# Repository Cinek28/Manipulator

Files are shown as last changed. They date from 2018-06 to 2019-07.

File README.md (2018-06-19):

# Manipulator
Repository designated for master's degree thesis development on manipulator's control problems. The thesis is conducted on real-life model of 6 DOF manipulator designated to work on Mars rover platform.

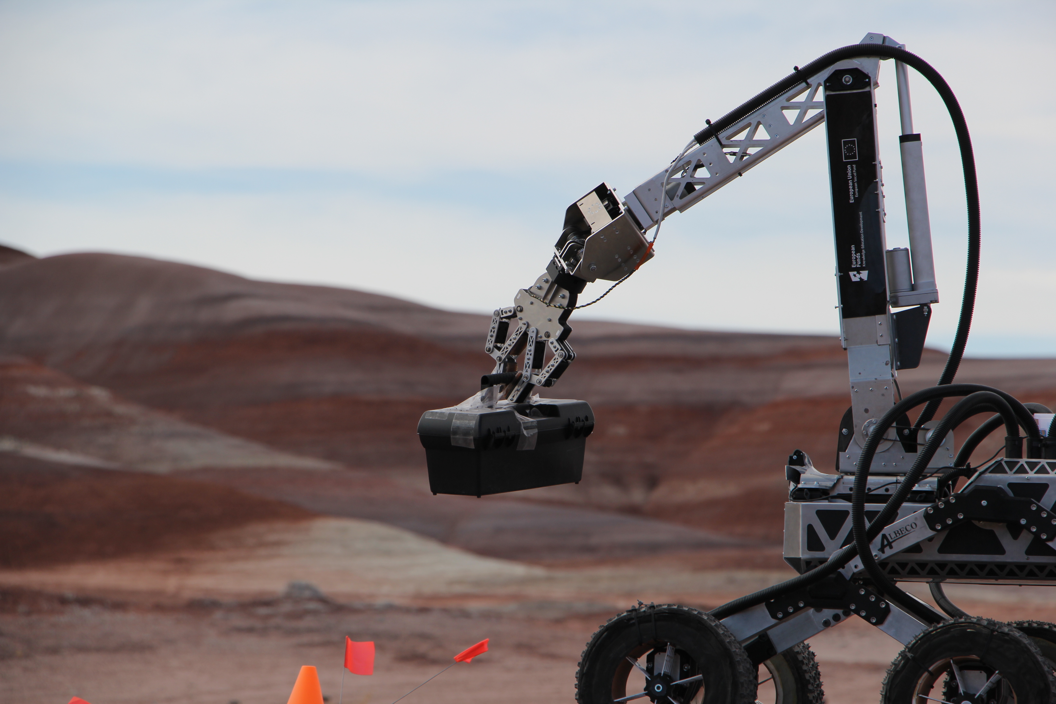
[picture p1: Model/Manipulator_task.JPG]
Manipulator working in designated environment on URC2018 competition.


List of folders:
1. Application: Contains project files of desktop app for controlling manipulator using UART connection.
2. Model: Contains renders and .stl files with whole manipulator model (able to open in CAD programs). Also a quick report of mechanical and electronic design of manipulator.
3. STM32F407: Folder containing Atollic TrueStudio project files and source code being developed for STM32F407RET microcontroller used to control manipulator
4. Simulation: Folder containing ROS files for simulation of manipulator's kinematics in Gazebo.
5. Thesis: Contains Latex files of the thesis.

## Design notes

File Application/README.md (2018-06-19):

# Application
Folder contains project files of desktop app, which is being desinged to use in order to control manipulator via UART/SSH connection. First app was written in C# (pic attached). Application in development will be written in C++ using Qt.

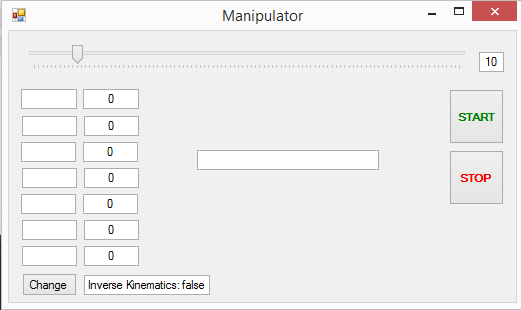
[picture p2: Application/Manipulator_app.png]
First control application for manipulator


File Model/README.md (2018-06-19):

# Model
Folder contains renders and pictures of manipulator. The review of mechanical and electronic design is called "Raport.pdf". Due to the fact that .stl file is large (> 100 MB) it is not held in remote repo. (STL file enables to view model in CAD programs)

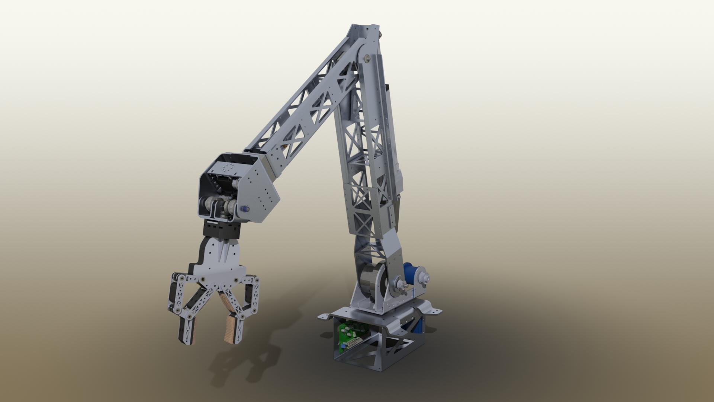
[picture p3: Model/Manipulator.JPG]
Render of manipulator's CAD model


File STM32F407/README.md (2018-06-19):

# STM32F407
The program written for STM32F407RET microcontroller using Atollic TrueStudio designed for controlling manipulator.

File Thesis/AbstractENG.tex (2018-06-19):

\externaldocument{CH_Wstep}
\externaldocument{CH_Opis_konstrukcji}
\externaldocument{CH_Model}
\externaldocument{CH_EKF}
\externaldocument{CH_Algorytm}

\begin{center}
\textbf{Abstract}
\end{center}
\paragraph{Implementation of Bellman-Ford algorithm for maze-solving by micromouse type robot}
\paragraph{}
The aim of this thesis was solving the shortest path problem for a maze described in the Micromouse competition rules along with the implementation of a chosen algorithm on a mobile robot. The document presents detailed description of project with the quality assessment of applied methods. First chapter shows requirements for Micromouse competition (Chapter 1). Based on the rules, a mechanical and electronic platform of mobile robot was developped (Chapter 2). Next step was to obtain mathematical model of given differential-drive robot (Chapter 3) which was used in chosen approach. These equations are essential in determining the position based on previously known location and measurements acquired from sensors installed on the platform. In order to localize the robot, a SLAM algorithm using Extended Kalman Filter was implemented (Chapter 4). The afore mentioned filter is recommended for estimating non- linear processes and enables the use of sensor fusion. This method gives an optimal information about process state. It is possible to point out where in the maze the robot is. Created map of environment is used in Bellman-Ford algorithm for finding the shortest path through the maze (Chapter 5). The final stage of the project was to conduct experiments in order to assess if the methods used were correct. Based on obtained results the weaknesses and possible improvements were summarized (Chapter 6).
\vspace*{\baselineskip}

\noindent\textbf{Keywords:} \textit{Micromouse, mobile robot, Bellman-Ford algorithm, shortest path problem, Extended Kalman Filter, localization}

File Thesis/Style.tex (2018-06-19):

%jezyk dokumentu
\usepackage[utf8]{inputenc}
\usepackage[T1]{fontenc}
\usepackage[T1]{polski}
\usepackage[english, polish]{babel}
%\setlanguage{polish}
\usepackage{fullpage}
\usepackage{pdfpages}
%Style
\usepackage{siunitx,booktabs,threeparttable,caption}
\captionsetup[table]{justification=raggedright,singlelinecheck=off}
\sisetup{separate-uncertainty=true}

\captionsetup[figure]{justification=centering,singlelinecheck=off}
\sisetup{separate-uncertainty=true}

\setlength\parindent{0.5cm}
\renewcommand{\baselinestretch}{1.15} 
\makeatletter
\def\ps@myPS{%
    \def\@oddfoot{\null\hfill\thepage}
    \def\@evenfoot{\thepage}%
    \def\@evenhead{\null\hfil\slshape\leftmark}%
    \def\@oddhead{{\slshape\rightmark}}}%
\makeatother
\makeatletter
\renewcommand\chapter{\if@openright\cleardoublepage\else\clearpage\fi
                    \thispagestyle{myPS}%
                    \global\@topnum\z@
                    \@afterindentfalse
                    \secdef\@chapter\@schapter}
\makeatother
\pagestyle{myPS}
%linkowanie
\usepackage{hyperref}
\hypersetup{
    colorlinks,
    citecolor=black,
    filecolor=black,
    linkcolor=black,
    urlcolor=black
}
\usepackage{multicol}
\usepackage{caption}
\usepackage{subcaption}
%math
\usepackage{amsmath}
\usepackage{gensymb}
\def\deg {$^o$\ }
\newcommand{\mat}[1]{\mathbf{#1}} % undergraduate algebra version
\newcommand{\sub}[1]{\footnotesize #1 \normalsize}
%bibliografia
\usepackage{csquotes}
\usepackage[backend=biber]{biblatex}
%,style=authoryear
%\renewcommand{\cite}[1]{\parencite{#1}}
\usepackage{float}
%numeracja
\usepackage{chngcntr}
%\counterwithout{figure}{chapter}	%numeracja ciagła
%oblsuga grafiki
\usepackage{graphicx}
\graphicspath{{../img/}{}../image/}
%time and date management
\usepackage{datetime}
\newcommand{\miesiac}{%
  \ifcase\THEMONTH
  \or Styczeń% 1
  \or Luty% 2
  \or Marzec% 3
  \or Kwiecień% 4
  \or Maj% 5
  \or Czerwiec% 6
  \or Lipiec% 7
  \or Sierpień% 8
  \or Wrzesień% 9
  \or Październik% 10
  \or Listopad% 11
  \or Grudzień% 12
  \fi}
\newdateformat{mmyyyy}{\miesiac \  \THEYEAR}

%zarzadzanie tekstem
\brokenpenalty=1000		% nie dziel wyrazów miedzy stronami
\clubpenalty=1000		% kara za sierotki
\widowpenalty=10000		% nie pozostawiaj wdów

\usepackage[inner=30mm,outer=20mm,top=25mm,bottom=25mm]{geometry}

%Wyliczenia:
\usepackage{enumerate}
%Fragmenty kodu:
\usepackage{listings}
\usepackage{color}

\definecolor{dkgreen}{rgb}{0,0.6,0}
\definecolor{gray}{rgb}{0.5,0.5,0.5}
\definecolor{mauve}{rgb}{0.58,0,0.82}

\lstset{frame=tb,
  language=C,
  aboveskip=3mm,
  belowskip=3mm,
  showstringspaces=false,
  columns=flexible,
  basicstyle={\small\ttfamily},
  numbers=none,
  numberstyle=\tiny\color{gray},
  keywordstyle=\color{blue},
  commentstyle=\color{dkgreen},
  stringstyle=\color{mauve},
  breaklines=true,
  breakatwhitespace=true,
  tabsize=3
}

\usepackage{xr}
\usepackage{amsfonts}
\defbibheading{myheading}[Bibliografia]{%
  \chapter*{#1}
  \addcontentsline{toc}{chapter}{#1}}

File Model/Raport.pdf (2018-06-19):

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

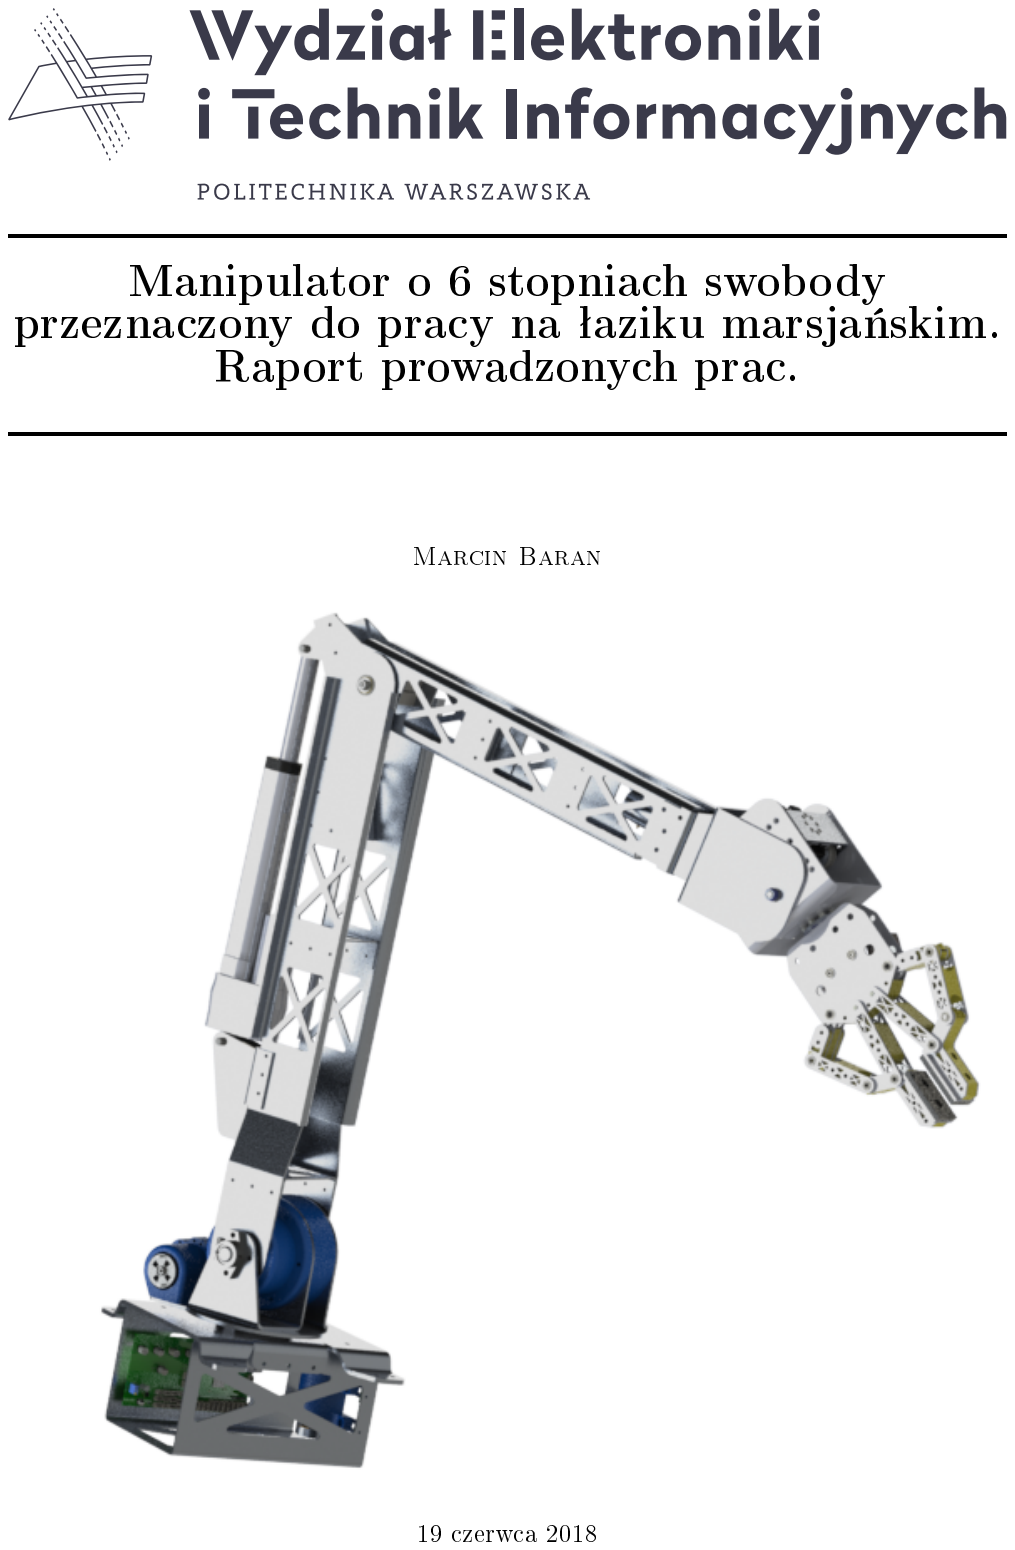
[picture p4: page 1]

# Spis tre±ci

## 0.1 Wst¦p

Manipulator zostaª skonstruowany oraz zbudowany z my±l¡ o pracy na ªaziku marsja«skim- projekcie Koªa Naukowego Robotyków realizowanego na zawody URC 2018. W obecnym etapie prac zako«czono monta» konstrukcji wykonanej z aluminium i ABS-X oraz przygotowano elektronik¦ potrzebn¡ do sterowania i zasilania nap¦dami ka»dego z czªonów mechanizmu. Manipulator b¦dzie tak»e platform¡ do badania efektywno±ci sterowania mechanizmu wieloczªonowego za pomoc¡ ró»nego typu regulatorów.

## 0.2 Mechanika

Manipulator posiada 6 stopni swobody realizowanych za pomoc¡:

- Stopie« I: Obrót podstawy

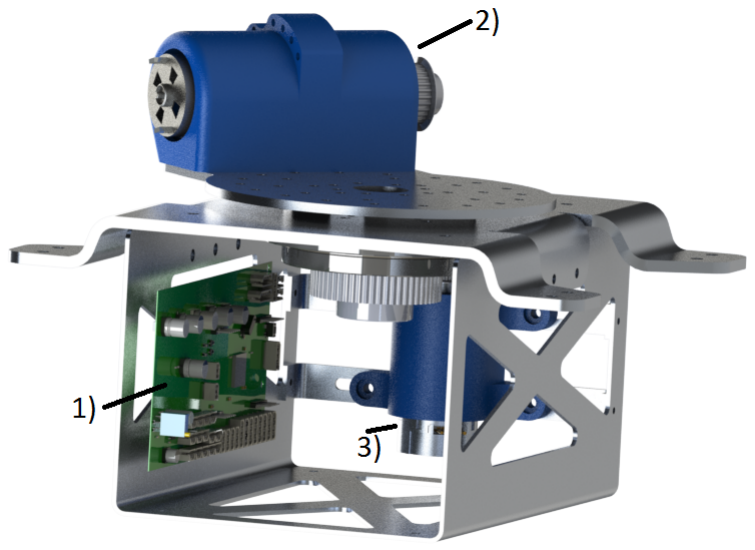
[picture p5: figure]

Obrót podstawy manipulatora realizowany jest za pomoc¡ silnika DC Pololu z przekªadni¡ 37Dx73L 131:1 zasilanym napi¦ciem 12V osi¡gaj¡cy pr¦dko±¢ obrotow¡ 80RPM (https://botland.com.pl/silniki-dc-z-przekladnia-i-enkoderami/5114-silnik-z-przekladnia-37dx73l-1311-enkoder-cpr-64.html) (https://botland.com.pl/silniki-dc-z-przekladnia-i-enkoderami/5114-silnik-z-przekladnia-37dx73l-1311-enkoder-cpr-64.html) (na powy»szej grace zaznaczony numerem 3). Przeªo»enie nap¦du na obrót podstawy jest realizowane za pomoc¡ paska HTD 3M oraz kóª z¦batych. Dodatkowo w podstawie manipulatora znajduje si¦ sterownik nap¦dów (oznaczony jako 1) pozwalaj¡cy na zasilanie oraz sterowanie wszystkimi nap¦dami za pomoc¡ sterowania sygnaªem PWM.

- Stopie« II: Obrót ramion

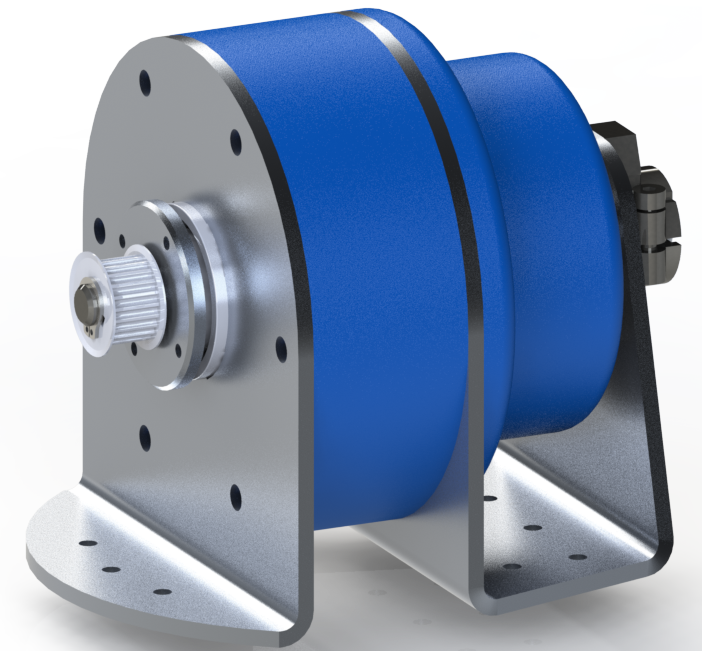
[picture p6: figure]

Obrót ramion realizowany jest za pomoc¡ przekªadni falowej o przeªo»eniu 159:1 oraz silnika od wkr¦tarki Bosch zasilanego napi¦ciem 12V (oznaczony na poprzedniej grace jako 2). Tutaj tak»e do poª¡czenia nap¦du z przekªadni¡ u»yto paska HTD oraz kóª z¦batych.

- Stopie« III: Obrót przedramienia

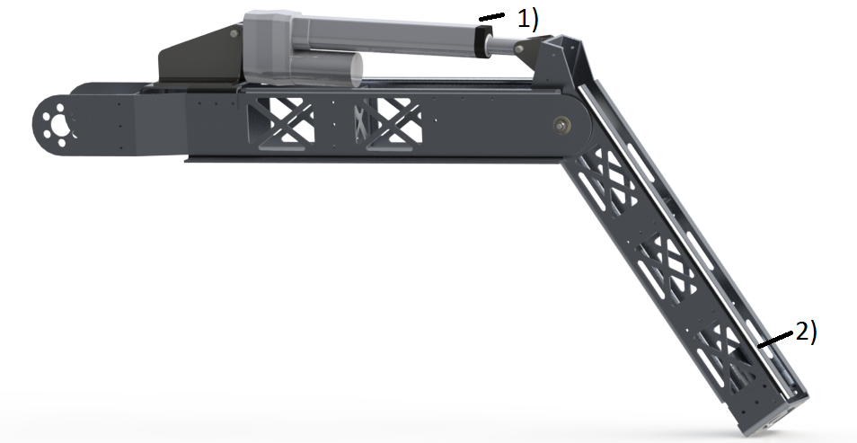
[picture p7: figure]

Obrót przedramienia wykonywany jest za pomoc¡ siªownika liniowego DSZY1 nap¦dzanego silnikiem DC 12V (http://www.drive-system.com/pdf/en/DC_Linearactuator_DSZY1_poti.pdf) o maksymalnym obci¡»eniu 1000N. (na grace zaznaczony jako 1).

- Stopie« IV: Obrót ki±ci

Obrót ki±ci sferycznej (nadgarstek) realizowany jest za pomoc¡ silnika DC Pololu z przekªadni¡ 37Dx73L 131:1 zasilanym napi¦ciem 12V osi¡gaj¡cy pr¦dko±¢ obrotow¡ 80RPM (https://botland.com.pl/silniki-dc-z-przekladnia-i-enkoderami/5114-silnik-z-przekladnia-37dx73l-1311-enkoder-cpr-64.html) (https://botland.com.pl/silniki-dc-z-przekladnia-i-enkoderami/5114-silnik-z-przekladnia-37dx73l-1311-enkoder-cpr-64.html) ( na grace powy»ej zaznaczone jako 2) poª¡czonego bezpo±rednio z ªo»yskiem obrotowym przymocowanym do ki±ci.

- Stopie« V i VI: Ki±¢ sferyczna

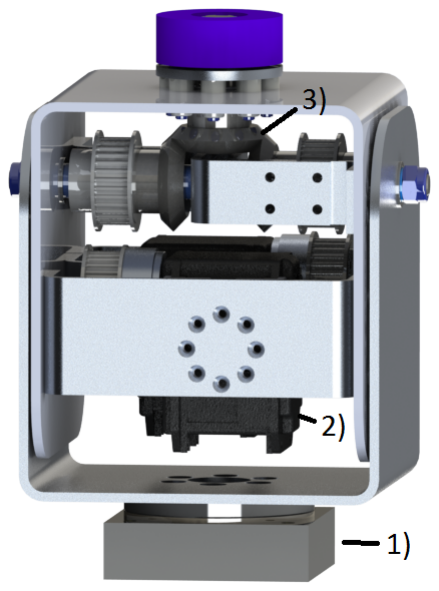
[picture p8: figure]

Ki±¢ sferyczna, czyli taka, w której osie obrotów czªonów pokrywaj¡ si¦ w jednym punkcie, zostaªa skonstruowana z wykorzystaniem mechanizmu ró»nicowego (dyferencjaªu) (3). Mechanizm nap¦dzany jest za pomoc¡ serw Dynamixel RX-64 o napi¦ciu zasilania od 15 do 18 V oraz momencie znamionowym 5.6 Nm (2) (http://www.trossenrobotics.com/dynamixel-rx-64-robotactuator.aspx). (http://www.trossenrobotics.com/dynamixel-rx-64-robot-actuator.aspx) Zastosowanie ki±ci sferycznej w znacznym stopniu uªatwia rozwi¡zanie zadania odwrotnego kinematyki pozwalaj¡cego na implementacj¦ sterowania w wygodniejszych wspóªrz¦dnych zwi¡zanych z narz¦dziem, a nie poszczególnymi czªonami.

## 0.3 Schemat elektroniczny

W celu zasilania nap¦dów manipulatora, a tak»e ich sterowania zostaªy zaprojektowane 2 pªytki PCB: sterownik nap¦dów oraz nakªadka pod pªytk¦ STM32 NUCLEO-F446RE, która posªu»y do sterowania, komunikacji oraz rozwi¡zywania zadania odwrotnego kinematyki. Jako sygnaª sprz¦»enia zwrotnego do regulatora nap¦dów posªu»y odczytywany z enkoderów magnetycznych, zamontowanych na ka»dym z czªonów, k¡t obrotu. W projekcie zastosowano enkodery rmy AMS: https://ams.com/kor/content/download/1285/7214/file/AS5040_DS000374_3-00.pdf. (https://ams.com/kor/content/download/1285/7214/file/AS5040_DS000374_3-00.pdf) Pozwala on na wyznaczanie absolutnej pozycji, co oznacza, »e nawet po wyª¡czeniu zasilania manipulatora i ponownym jego wª¡czeniu b¦dzie mo»-liwe wyznaczenie dokªadnej konguracji mechanizmu. Komunikacja z komputerem pokªadowym ªazika odbywa¢ si¦ b¦dzie za pomoc¡ interfejsu CAN. Do komunikacji z komputerem w celach implementacji oprogramowania zastosowany zostanie interfejs UART.

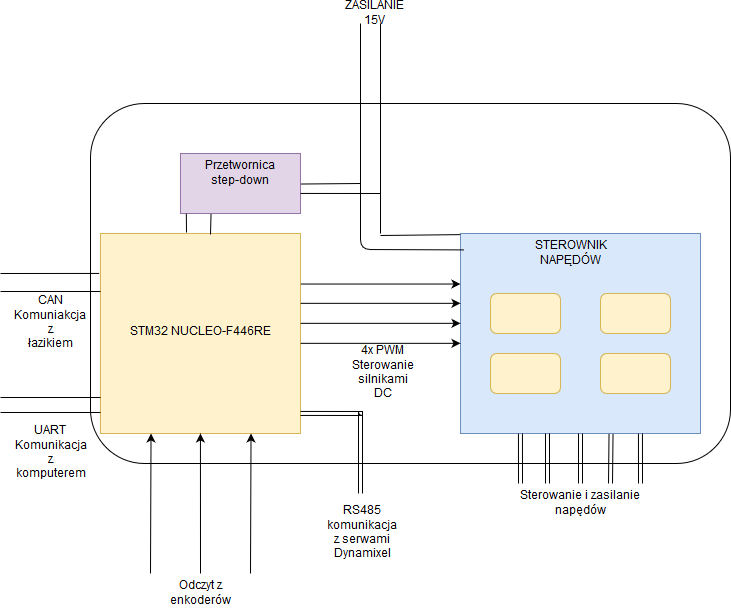
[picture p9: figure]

## 0.4 Sterowanie

Na tym etapie zostaªo stworzone oprogramowanie steruj¡ce pozwalaj¡ce na sterowanie we wspóªrz¦dnych zª¡czowych oraz kod pozwalaj¡cy na zastosowanie kinematyki odwrotnej w celu sterowania we wspóªrz¦dnych narz¦dziowych (zwi¡zanych z chwytakiem). W tej chwili trwa integracja czujników magnetycznych (enkoderów) w celu wyliczania pr¦dko±ci czªonów i zako«czenia implementacji programu steruj¡cego.

## 0.5 Plan dalszych prac

Prace nad oprogramowaniem i symulacj¡ pracy manipulatora zostaªy opó¹nione ze wzgl¦du na konieczno±¢ poprawy konstrukcji mechanicznej w okresie kwiecie«-czerwiec. Na ten moment prace nad konstrukcj¡ mechaniczn¡ zostaªy zako«czone. Plan pracy przedstawia si¦ nast¦puj¡co:

- do 30 czerwca: uko«czenie integracji enkoderów magnetycznych
- do 15 lipca: utworzenie modelu manipulatora w Gazebo - przesªanie kolejnego raportu
- do 30 lipca: przeprowadzenie symulacji dziaªania mechanizmu w Gazebo
- do 15 sierpnia: uko«czenie pisania programu steruj¡cego manipulatorem
- do 30 sierpnia: napisanie aplikacji desktopowej do sterowania i debugowania pracy manipulatora -
| przesªanie kolejnego raportu
- od wrze±nia: badanie i dostosowywanie metod sterowania (cz¦±¢ badawcza)
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

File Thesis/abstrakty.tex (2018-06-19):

%!TeX spellcheck = pl_PL
\documentclass[11pt, a4paper, twoside]{report}

\input{Style.tex}
\addbibresource{./Bibliografia/books.bib}
%\addbibresource{../bib/articles.bib}
\addbibresource{./Bibliografia/online.bib}

\begin{document}
%\input{nauka.tex}

%\input{TitlePage2017.tex}
%\newpage\null\thispagestyle{empty}
%\newpage\null\thispagestyle{empty}
%\input{AbstractPL.tex}
%\newpage\null\thispagestyle{empty}
%\newpage\null\thispagestyle{empty}
\pagenumbering{gobble}
\input{AbstractPL.tex}

%\newpage\null\thispagestyle{empty}
%\input{Oswiadczenie.tex}
%\newpage\null\thispagestyle{empty}

%\tableofcontents
%\thispagestyle{empty}

%\addtocontents{toc}{\protect%\thispagestyle{empty}}

%\input{CH_Wstep.tex}
%\input{CH_Opis_konstrukcji.tex}
%\input{CH_Model.tex}
%\input{CH_EKF.tex}
%\input{CH_Algorytm.tex}
%\input{CH_Wnioski.tex}

%\cleardoublepage
%bibliograpy
%bibintoc
%\printbibheading[title={Bibliography},heading=bibnumbered]
%\nocite{*}
%\printbibliography[heading=myheading]

%\clearpage
%\addcontentsline{toc}{chapter}%{\listfigurename}
%\listoffigures

%\addcontentsline{toc}{chapter}%{\listtablename}
%\listoftables

%\appendix
%\input{CH_Zalaczniki.tex}

\end{document}

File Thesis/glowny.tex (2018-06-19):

%!TeX spellcheck = pl_PL
\documentclass[11pt, a4paper, twoside]{report}

\input{Style.tex}
\addbibresource{./Bibliografia/books.bib}
%\addbibresource{../bib/articles.bib}
\addbibresource{./Bibliografia/online.bib}

\begin{document}

%\input{TitlePage2018.tex}
%\newpage\null\thispagestyle{empty}
%\newpage\null\thispagestyle{empty}
\input{AbstractPL.tex}
\newpage\null\thispagestyle{empty}
\newpage\null\thispagestyle{empty}
\input{AbstractENG.tex}
\newpage\null\thispagestyle{empty}
\input{Oswiadczenie.tex}
\newpage\null\thispagestyle{empty}

\tableofcontents
\thispagestyle{empty}

\addtocontents{toc}{\protect\thispagestyle{empty}}

\input{CH_Wstep.tex}
\input{CH_Stan_wiedzy.tex}
\input{CH_Opis_konstrukcji_manipulatora.tex}
\input{CH_Model_kinematyki_manipulatora.tex}
\input{CH_Symulacja_konstrukcji_w_środowisku_Gazebo.tex}
\input{CH_Program_sterujacy_ruchem_robota.tex}
\input{CH_Badanie_jakości_sterowania.tex}
\input{CH_Wnioski.tex}

\cleardoublepage
%bibliograpy
%bibintoc
%\printbibheading[title={Bibliography},heading=bibnumbered]
\nocite{*}
\printbibliography[heading=myheading]

\clearpage
\addcontentsline{toc}{chapter}{\listfigurename}
\listoffigures

\addcontentsline{toc}{chapter}{\listtablename}
\listoftables

\appendix
%\input{CH_Zalaczniki.tex}

\end{document}

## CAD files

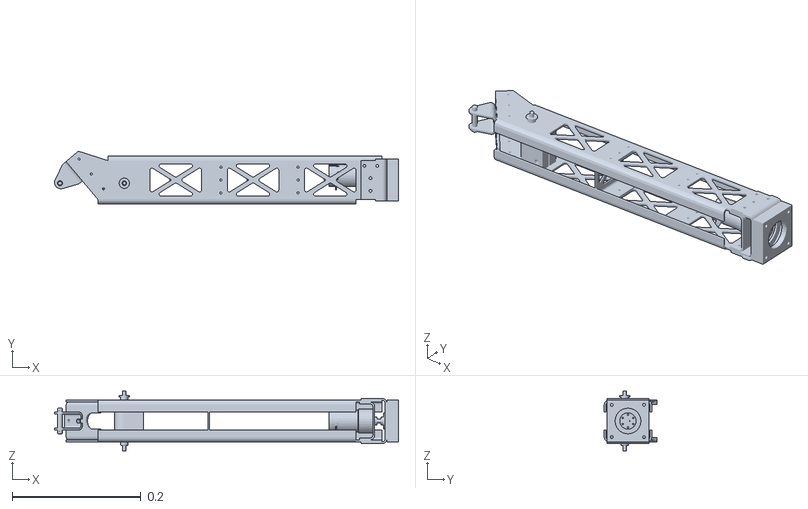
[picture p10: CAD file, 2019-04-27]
Simulation/src/manipulator/meshes/arm_link.STL
0.534 x 0.0818 x 0.0925

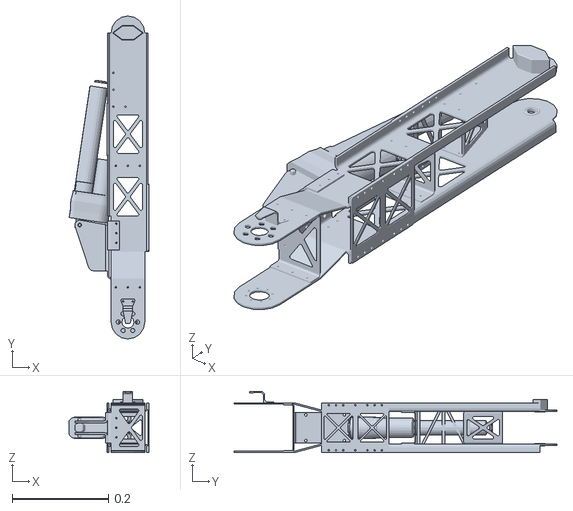
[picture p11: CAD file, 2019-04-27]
Simulation/src/manipulator/meshes/forearm_link.STL
0.165 x 0.67 x 0.127

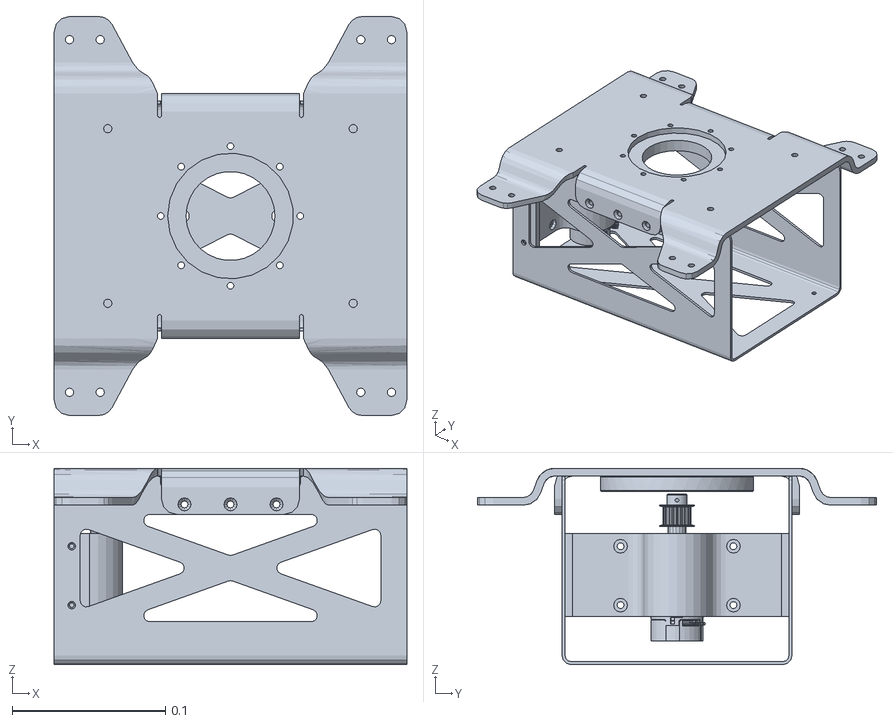
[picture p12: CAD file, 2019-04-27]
Simulation/src/manipulator/meshes/base_link.STL
0.23 x 0.26 x 0.128

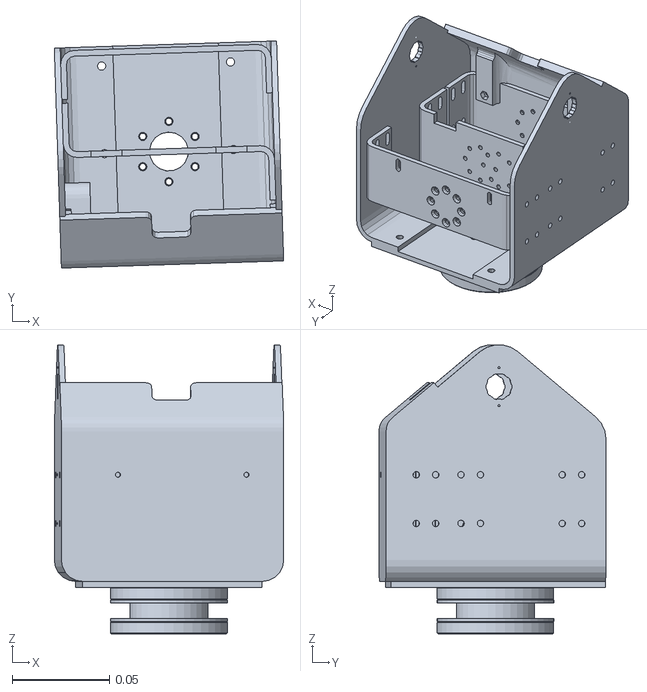
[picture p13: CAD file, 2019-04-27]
Simulation/src/manipulator/meshes/wrist_rotation_link.STL
0.118 x 0.117 x 0.148

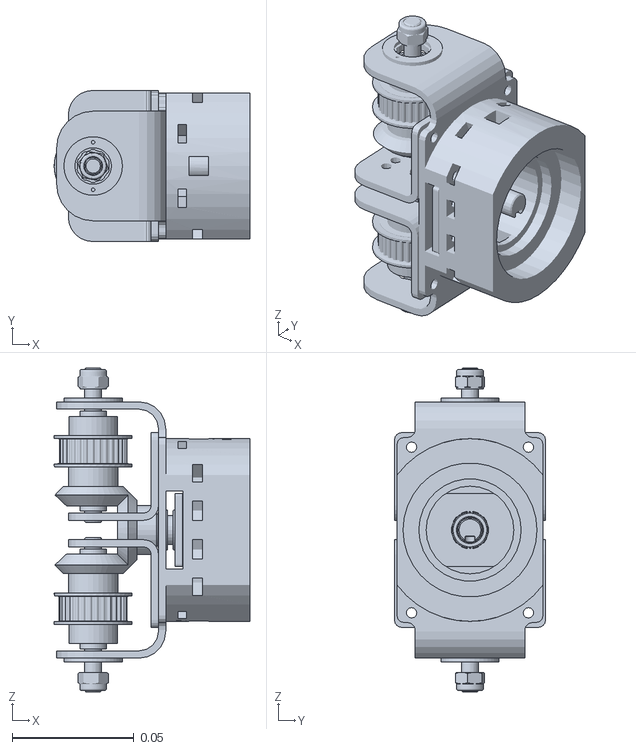
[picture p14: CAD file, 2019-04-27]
Simulation/src/manipulator/meshes/wrist_pitch_link.STL
0.0803 x 0.062 x 0.133

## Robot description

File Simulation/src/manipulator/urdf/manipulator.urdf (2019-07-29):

<robot name="manipulator">

  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
  <link name="world"/>

  <joint name="fixed" type="fixed">
    <parent link="world"/>
    <child link="base_link"/>
  </joint>

  <link name="base_link">
    <inertial>
      <origin xyz="-0.029 3.0957E-06 0.081458" rpy="0 0 0" />
      <mass value="1.404" />
      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
    </inertial>
    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
  </link>

 <link name="shoulder_link">
    <inertial>
      <origin xyz="-0.024603 0.0034265 0.064143" rpy="0 0 0" />
      <mass value="4.1214" />
      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
    </inertial>
    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
  </link>

  <joint name="shoulder_rotation" type="revolute">
    <origin xyz="0 0 0.13" rpy="0 0 0" />
    <parent link="base_link" />
    <child link="shoulder_link" />
    <axis xyz="0 0 1" />
    <limit lower="-3.14" upper="3.14" effort="50" velocity="8.3776" />
  </joint>

  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

  <link name="forearm_link">
    <inertial>
      <origin xyz="-0.030709 0.2846 0.0021162" rpy="0 0 0" />
      <mass value="2.138" />
      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
    </inertial>
    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
  </link>

  <joint name="forearm_rotation" type="revolute">
    <origin xyz="0 0.00175 0.0705" rpy="1.5708 0 0" />
    <parent link="shoulder_link" />
    <child link="forearm_link" />
    <axis xyz="0 0 -1" />
    <limit lower="-0.90" upper="1.3963" effort="500" velocity="1.2" />
  </joint>

  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

  <link name="arm_link">
    <inertial>
      <origin xyz="0.1767 0.0069722 5.0223E-06" rpy="0 0 0" />
      <mass value="1.1195" />
      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
    </inertial>
    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
  </link>

  <joint name="arm_rotation" type="revolute">
    <origin xyz="0 0.6 0" rpy="0 0 -1.3089" />
    <parent link="forearm_link" />
    <child link="arm_link" />
    <axis xyz="0 0 -1" />
    <limit lower="-2.5" upper="0" effort="500" velocity="0.2" />
  </joint>

  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

  <link name="wrist_rotation_link">
    <inertial>
      <origin xyz="0.00022986 -0.0044455 0.068045" rpy="0 0 0" />
      <mass value="0.70662" />
      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
    </inertial>
    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
  </link>

  <joint name="wrist_rotation" type="revolute">
    <origin xyz="0.408 0.005 0" rpy="0 1.5708 0" />
    <parent link="arm_link" />
    <child link="wrist_rotation_link" />
    <axis xyz="0 0 -1" />
    <limit lower="-3.14" upper="3.14" effort="18" velocity="8.3776" />
  </joint>

 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

  <link name="wrist_pitch_link">
    <inertial>
      <origin xyz="0.02283 1.6924E-05 4.4001E-05" rpy="0 0 0" />
      <mass value="0.22279" />
      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
    </inertial>
    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
  </link>

  <joint name="wrist_pitch" type="revolute">
    <origin xyz="0 0 0.129" rpy="-1.5708 0 1.603" />
    <parent link="wrist_rotation_link" />
    <child link="wrist_pitch_link" />
    <axis xyz="0 0 -1" />
    <limit lower="0" upper="3.14" effort="10.8" velocity="5.236" />
  </joint>

 <link name="gripper_link">
    <inertial>
      <origin xyz="0.00062878 0.0062787 0.096632" rpy="0 0 0" />
      <mass value="0.52227" />
      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
    </inertial>
    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
  </link>

  <joint name="gripper_rotation" type="revolute">
    <origin xyz="0.0643 0 0" rpy="0 1.5708 0" />
    <parent link="wrist_pitch_link" />
    <child link="gripper_link" />
    <axis xyz="0 0 -1" />
    <limit lower="-3.14" upper="3.14" effort="10.8" velocity="5.236" />
  </joint>

  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

</robot>

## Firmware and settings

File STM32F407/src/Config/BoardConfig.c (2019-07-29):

/*
 * BoardConfig.c
 *
 *  Created on: 21.07.2019
 *      Author: Cinek
 */

#include "BoardConfig.h"

uint8_t RCC_CONF()
{
	// Setting HSE with 8MHz external oscillator as main clock:
	RCC_DeInit();

	RCC_HSEConfig(RCC_HSE_ON);
	while(RCC_WaitForHSEStartUp() != SUCCESS);

	// Setting frequency to 144 MHz:
	RCC_PLLConfig(RCC_PLLSource_HSE, 4, 144, 2, 4);
	RCC_HCLKConfig(RCC_SYSCLK_Div1);
	// PCLK1 peripherals at 36 MHz:
	RCC_PCLK1Config(RCC_HCLK_Div4);
	// PCLK2 peripherals at 72 MHz:
	RCC_PCLK2Config(RCC_HCLK_Div2);
	RCC_SYSCLKConfig(RCC_SYSCLKSource_PLLCLK);
	//SysTick initialisation to 1000 Hz:
//	SysTick_Config(SYSTIC_CNT);

	SystemCoreClockUpdate();

	RCC_ClocksTypeDef RCC_Clocks;
	RCC_GetClocksFreq(&RCC_Clocks);
	if(RCC_Clocks.HCLK_Frequency != CORE_CLK_FREQ)
		return -1;
	else if(SystemCoreClock != CORE_CLK_FREQ)
		return -2;
	else if(RCC_Clocks.HCLK_Frequency != 36000000)
		return -3;
	else if(RCC_Clocks.HCLK_Frequency != 72000000)
		return -4;

	RCC_PLLCmd(ENABLE);
	while(RCC_GetFlagStatus(RCC_FLAG_PLLRDY) != SET);
	return 0;
};

void GPIO_MOTOR_CONF(){

	RCC_AHB1PeriphClockCmd(RCC_AHB1Periph_GPIOA, ENABLE);
	RCC_AHB1PeriphClockCmd(RCC_AHB1Periph_GPIOB, ENABLE);
	RCC_AHB1PeriphClockCmd(RCC_AHB1Periph_GPIOC, ENABLE);
	RCC_AHB1PeriphClockCmd(RCC_AHB1Periph_GPIOD, ENABLE);
	RCC_AHB1PeriphClockCmd(RCC_AHB1Periph_GPIOE, ENABLE);

	//MOTOR_1_PWM:

	GPIO_InitTypeDef GPIO_InitStructure;
	GPIO_InitStructure.GPIO_Pin = GPIO_Pin_8;
	GPIO_InitStructure.GPIO_OType = GPIO_OType_PP;
	GPIO_InitStructure.GPIO_PuPd = GPIO_PuPd_NOPULL;
	GPIO_InitStructure.GPIO_Mode = GPIO_Mode_AF;
	GPIO_InitStructure.GPIO_Speed = GPIO_Speed_100MHz;
	GPIO_Init(GPIOB, &GPIO_InitStructure);
	GPIO_PinAFConfig(GPIOB, GPIO_PinSource8, GPIO_AF_TIM4);

	//MOTOR_2_PWM:

	GPIO_InitStructure.GPIO_Pin = GPIO_Pin_2;
	GPIO_Init(GPIOA, &GPIO_InitStructure);
	GPIO_PinAFConfig(GPIOA, GPIO_PinSource2, GPIO_AF_TIM2);

	GPIO_InitStructure.GPIO_Pin = GPIO_Pin_6;
    GPIO_Init(GPIOA, &GPIO_InitStructure);
	GPIO_PinAFConfig(GPIOA, GPIO_PinSource6, GPIO_AF_TIM3);

	//MOTOR_3_PWM:

	GPIO_InitStructure.GPIO_Pin = GPIO_Pin_3;
	GPIO_Init(GPIOA, &GPIO_InitStructure);
	GPIO_PinAFConfig(GPIOA, GPIO_PinSource2, GPIO_AF_TIM2);

	//MOTOR_4_PWM:

	GPIO_InitStructure.GPIO_Pin = GPIO_Pin_15;
	GPIO_Init(GPIOA, &GPIO_InitStructure);
	GPIO_PinAFConfig(GPIOA, GPIO_PinSource15, GPIO_AF_TIM2);

	//MOTOR_5_PWM:

	GPIO_InitStructure.GPIO_Pin = GPIO_Pin_3;
	GPIO_Init(GPIOB, &GPIO_InitStructure);
	GPIO_PinAFConfig(GPIOB, GPIO_PinSource3, GPIO_AF_TIM2);

	//MOTOR_6_PWM:

	GPIO_InitStructure.GPIO_Pin = GPIO_Pin_9;
	GPIO_Init(GPIOB, &GPIO_InitStructure);
	GPIO_PinAFConfig(GPIOB, GPIO_PinSource9, GPIO_AF_TIM4);

	//BM_PWM:

	GPIO_InitStructure.GPIO_Pin = GPIO_Pin_10;
	GPIO_Init(GPIOB, &GPIO_InitStructure);
	GPIO_PinAFConfig(GPIOB, GPIO_PinSource10, GPIO_AF_TIM2);

	GPIO_InitStructure.GPIO_Pin = GPIO_Pin_11;
	GPIO_Init(GPIOB, &GPIO_InitStructure);
	GPIO_PinAFConfig(GPIOB, GPIO_PinSource11, GPIO_AF_TIM2);

	//Servo PWM:

	GPIO_InitStructure.GPIO_Pin = GPIO_Pin_4 | GPIO_Pin_5;
	GPIO_Init(GPIOB, &GPIO_InitStructure);
	GPIO_PinAFConfig(GPIOB, GPIO_PinSource4, GPIO_AF_TIM3);
	GPIO_PinAFConfig(GPIOB, GPIO_PinSource5, GPIO_AF_TIM3);

	//MOTOR_1_IN gripper:

	GPIO_InitStructure.GPIO_Pin = GPIO_Pin_2 | GPIO_Pin_3;
	GPIO_InitStructure.GPIO_Mode = GPIO_Mode_OUT;
	GPIO_Init(GPIOE, &GPIO_InitStructure);
	GPIO_ResetBits(GPIOE, GPIO_Pin_3);
	GPIO_ResetBits(GPIOE, GPIO_Pin_2);

	//MOTOR_2_IN gripper:

	GPIO_InitStructure.GPIO_Pin = GPIO_Pin_13 | GPIO_Pin_14;
	GPIO_InitStructure.GPIO_Mode = GPIO_Mode_OUT;
	GPIO_Init(GPIOC, &GPIO_InitStructure);
	GPIO_ResetBits(GPIOC, GPIO_Pin_13);
	GPIO_ResetBits(GPIOC, GPIO_Pin_14);

	/*//MOTOR_3_IN:

	GPIO_InitStructure.GPIO_Pin = GPIO_Pin_15;
	GPIO_InitStructure.GPIO_Mode = GPIO_Mode_OUT;
	GPIO_Init(GPIOC, &GPIO_InitStructure);
	GPIO_ResetBits(GPIOC, GPIO_Pin_15);

	GPIO_InitStructure.GPIO_Pin = GPIO_Pin_2;
	GPIO_InitStructure.GPIO_Mode = GPIO_Mode_OUT;
	GPIO_Init(GPIOD, &GPIO_InitStructure);
	GPIO_ResetBits(GPIOD, GPIO_Pin_2);*/

	//MOTOR_4_IN (first degree):

	GPIO_InitStructure.GPIO_Pin = GPIO_Pin_0 | GPIO_Pin_1;
	GPIO_InitStructure.GPIO_Mode = GPIO_Mode_OUT;
	GPIO_Init(GPIOD, &GPIO_InitStructure);
	GPIO_SetBits(GPIOD, GPIO_Pin_0);
	GPIO_ResetBits(GPIOD, GPIO_Pin_1);

	//MOTOR_5_IN: (third degree)

	GPIO_InitStructure.GPIO_Pin = GPIO_Pin_4 | GPIO_Pin_7;
	GPIO_InitStructure.GPIO_Mode = GPIO_Mode_OUT;
	GPIO_Init(GPIOD, &GPIO_InitStructure);
	GPIO_SetBits(GPIOD, GPIO_Pin_4);
	GPIO_ResetBits(GPIOD, GPIO_Pin_7);

	//MOTOR_6_IN: (fourth degree)

	GPIO_InitStructure.GPIO_Pin = GPIO_Pin_0 | GPIO_Pin_4;
	GPIO_InitStructure.GPIO_Mode = GPIO_Mode_OUT;
	GPIO_Init(GPIOE, &GPIO_InitStructure);
	GPIO_SetBits(GPIOE, GPIO_Pin_4);
	GPIO_ResetBits(GPIOE, GPIO_Pin_0);

	//BM_ENABLE: (second degree)
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

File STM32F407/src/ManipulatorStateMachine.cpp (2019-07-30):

/*
 * ManipulatorStateMachine.cpp
 *
 *  Created on: Jul 11, 2019
 *      Author: mrbr
 */

#include <stdio.h>

#include "ManipulatorStateMachine.h"

const char* stateToStr(State state)
{
	switch(state)
	{
	case INIT_STATE:
		return "INIT_STATE";
	case RESET_STATE:
		return "RESET_STATE";
	case IDLE_STATE:
		return "IDLE_STATE";
	case JOINT_STATE:
		return "JOINT_STATE";
	case TOOL_STATE:
		return "TOOL_STATE";
	case TEST_STATE:
		return "TEST_STATE";
	default:
		return "UNKNOWN";
	}
}

ManipulatorStateMachine::ManipulatorStateMachine()
{
	stateHandlers[INIT_STATE] = runInit;
	stateHandlers[RESET_STATE] = runReset;
	stateHandlers[IDLE_STATE] = runIdle;
	stateHandlers[JOINT_STATE] = runJointMode;
	stateHandlers[TOOL_STATE] = runToolMode;
	stateHandlers[TEST_STATE] = runTestMode;

	joints[0] = &shoulder;
	joints[1] = &forearm;
	joints[2] = &arm;
	joints[3] = &wristRotation;
	joints[4] = &wristPitch;
	joints[5] = &gripperRotation;
}

uint8_t ManipulatorStateMachine::init()
{
	USART1_CONF();
	USART1_DXL_CONF(BAUDRATE);
	USART2_CONF();
	GPIO_MOTOR_CONF();
	TIM_PWM_CONF();

	shoulder.init(&TIM2->CCR1, &TIM5->CNT, GPIOD, GPIO_Pin_0, GPIO_Pin_1);
	shoulder.setMaxVelocity(8.378);
	shoulder.setEncoderRange(ENCODER_RANGE_HIGH);
	shoulder.setRatio(0.5);
	shoulder.initPID(400, 300, 1);

	forearm.init(&TIM2->CCR3, &TIM2->CCR4, &TIM3->CNT);
	forearm.setMaxVelocity(8.378);
	forearm.setEncoderRange(ENCODER_RANGE_LOW);
	forearm.setRatio(1.0);
	forearm.initPID(200, 100, 0);

	arm.init(&TIM2->CCR2, &TIM1->CNT, GPIOD, GPIO_Pin_4, GPIO_Pin_7);
	arm.setMaxVelocity(1.0);
	arm.setEncoderRange(ENCODER_RANGE_LOW);
	arm.setRatio(1.0);
	arm.initPID(200, 100, 0);

	wristRotation.init(&TIM4->CCR4, &TIM8->CNT, GPIOE, GPIO_Pin_0, GPIO_Pin_4);
	wristRotation.setMaxVelocity(8.378);
	wristRotation.setEncoderRange(ENCODER_RANGE_HIGH);
	wristRotation.setRatio(1.0);
	wristRotation.initPID(200, 300, 0);

	wristPitch.init(1);
	wristPitch.setMaxVelocity(6.702);
	wristPitch.setRatio(1.0);
	wristPitch.initPID(200, 100, 0);

	gripperRotation.init(2);
	gripperRotation.setMaxVelocity(6.702);
	gripperRotation.setRatio(1.0);
	gripperRotation.initPID(200, 100, 0);

	gripper.init(&TIM4->CCR3, nullptr, GPIOE, GPIO_Pin_2, GPIO_Pin_3);
	gripper.setMaxVelocity(8.378);
	gripper.setRatio(1.0);

	_INFO("Initialized main board peripherals.");
	_INFO("Initialized manipulator motors.");
	return 1;
}

void ManipulatorStateMachine::setJointsVel(const double* velocities)
{
	for(int i = 0; i < NUM_JOINTS; ++i)
	{
		joints[i]->setVelocity(velocities[i]);
	}
}

void ManipulatorStateMachine::setMode(MODE mode)
{
	for(int i = 0; i < NUM_JOINTS; ++i)
	{
		joints[i]->setMode(mode);
	}
}

void ManipulatorStateMachine::emergencyStop()
{
	for(int i = 0; i < NUM_JOINTS; ++i)
	{
		joints[i]->setVelocity(0.0);
	}
	_WARN("Stopped all motors");
}

void ManipulatorStateMachine::closeGripper(const double& velocity)
{
	gripper.setVelocity(velocity);
	_INFO("Closing gripper");
}

void ManipulatorStateMachine::openGripper(const double& velocity)
{
	gripper.setVelocity(-velocity);
	_INFO("Opening gripper");
}

State ManipulatorStateMachine::getCurrentState()
{
	return currentState;
}

bool ManipulatorStateMachine::run()
{
	if(currentState != INIT_STATE)
	{
		_ERR("Manipulator not initialized!");
		return false;
	}

	_INFO("Starting manipulator control.");
	while(!runOnce());
	return true;
}

bool ManipulatorStateMachine::runOnce()
{
	State tempState = stateHandlers[currentState]((void*)this);

	if(currentState == endState)
	{
		emergencyStop();
		_WARN("End state met- exiting state machine");
		return true;
	}

	if(tempState != currentState)
	{
		emergencyStop();
		_WARN("Changing state from %s to %s", stateToStr(currentState), stateToStr(tempState));
		currentState = tempState;
	}
	return false;
}

State runInit(void* params)
{
	ManipulatorStateMachine* manipulator = (ManipulatorStateMachine*)params;
	if(!manipulator->init())
		return RESET_STATE;

	return JOINT_STATE;
}

State runReset(void* params)
{
	ManipulatorStateMachine* manipulator = (ManipulatorStateMachine*)params;
	manipulator->emergencyStop();
	xTaskNotifyWait(0, 0, NULL, portMAX_DELAY);
	if(xQueueReceive(usartQueue, (void*) &(manipulator->msgReceived), TIMEOUT/portTICK_PERIOD_MS))
	{
		switch(manipulator->msgReceived.type)
		{
			case JOINT ... TEST:
			{
				return manipulator->msgReceived.type;
			}
			default:
				return IDLE_STATE;
		}
	}
	return RESET_STATE;
}

State runIdle(void* params)
{
	ManipulatorStateMachine* manipulator = (ManipulatorStateMachine*)params;;
	if(xQueueReceive(usartQueue, (void*) &(manipulator->msgReceived), 0))
	{
		switch(manipulator->msgReceived.type)
		{
			case JOINT ... TEST:
			{
				return manipulator->msgReceived.type;
			}
			default:
				return IDLE_STATE;
		}
	}

	return IDLE_STATE;
}

State runJointMode(void* params)
{
	ManipulatorStateMachine* manipulator = (ManipulatorStateMachine*)params;
	if(xQueueReceive(usartQueue, (void*) &(manipulator->msgReceived), TIMEOUT/portTICK_PERIOD_MS))
	{
		switch(manipulator->msgReceived.type)
		{
			case JOINT:
			{
				double vels[NUM_JOINTS];
				for(int i = 0; i < manipulator->msgReceived.length/2; ++i)
				{
					vels[i] = (double)(manipulator->msgReceived.params[i] |
									   manipulator->msgReceived.params[i+1] << 8);
					manipulator->setMode(PID);
				}
				manipulator->setJointsVel(vels);
				return JOINT_STATE;
			}
			case TOOL ... TEST:
			{
				return manipulator->msgReceived.type;
			}
			default:
				return IDLE_STATE;
		}
	}
	return IDLE_STATE;
}

State runToolMode(void* params)
{
	ManipulatorStateMachine* manipulator = (ManipulatorStateMachine*)params;
	if(xQueueReceive(usartQueue, (void*) &(manipulator->msgReceived), TIMEOUT/portTICK_PERIOD_MS))
	{
		switch(manipulator->msgReceived.type)
		{
		case TOOL:
		{
			double vels[NUM_JOINTS];
			for(int i = 0; i < manipulator->msgReceived.length/2; ++i)
			{
				vels[i] = (double)(manipulator->msgReceived.params[i] |
						           manipulator->msgReceived.params[i+1] << 8);
				manipulator->setMode(PID);
			}
			manipulator->setJointsVel(vels);
			return TOOL_STATE;
		}
		case JOINT:
		{
			return JOINT_STATE;
		}
		case TEST:
		{
			return TEST_STATE;
		}
		default:
			return IDLE_STATE;
		}
	}
	return IDLE_STATE;
}

State runTestMode(void* params)
{
	ManipulatorStateMachine* manipulator = (ManipulatorStateMachine*)params;
	if(xQueueReceive(usartQueue, (void*) &(manipulator->msgReceived), TIMEOUT/portTICK_PERIOD_MS))
	{
		switch(manipulator->msgReceived.type)
		{
		case TOOL:
		{
			double vels[NUM_JOINTS];
			for(int i = 0; i < manipulator->msgReceived.length/2; ++i)
			{
				vels[i] = (double)(manipulator->msgReceived.params[i] |
								   manipulator->msgReceived.params[i+1] << 8);
				manipulator->setMode(FREE);
			}
			manipulator->setJointsVel(vels);
			return TOOL_STATE;
		}
		case JOINT:
		{
			return JOINT_STATE;
		}
		case TEST:
		{
			return TEST_STATE;
		}
		default:
			return IDLE_STATE;
		}
	}
	return IDLE_STATE;
}

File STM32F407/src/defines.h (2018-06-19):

#ifndef DEFINES_H_
#define DEFINES_H_

//LEDS:

#define LED_GREEN 37
#define LED_YELLOW 98

//Encoders pinout:

#define ENK_1_A 4
#define ENK_1_B 5
#define ENK_2_A 23
#define ENK_2_B 24
#define ENK_3_A 40
#define ENK_3_B 42
#define ENK_4_A 53
#define ENK_4_B 54
#define ENK_5_A 59
#define ENK_5_B 60
#define ENK_6_A 63
#define ENK_6_B 64
#define ENK_7_A 90
#define ENK_7_B 91

//Motors current measurement:

#define MOTOR_1_CURRENT 18
#define MOTOR_2_CURRENT 25
#define MOTOR_3_CURRENT 26
#define MOTOR_4_CURRENT 15
#define MOTOR_5_CURRENT 16
#define MOTOR_6_CURRENT 17
#define BM_CURRENT 30

//Motors direction pins:

#define MOTOR_1_INA 1
#define MOTOR_1_INB 2
#define MOTOR_2_INA 8
#define MOTOR_2_INB 7
#define MOTOR_3_INA 83
#define MOTOR_3_INB 9
#define MOTOR_4_INA 82
#define MOTOR_4_INB 81
#define MOTOR_5_INA 88
#define MOTOR_5_INB 85
#define MOTOR_6_INA 3
#define MOTOR_6_INB 97

//Motors PWM outputs:

#define MOTOR_1_PWM 95
#define MOTOR_2_PWM 25
#define MOTOR_3_PWM 26
#define MOTOR_4_PWM 77
#define MOTOR_5_PWM 89
#define MOTOR_6_PWM 96

//High power motor pinout:

#define BM_L_PWM 48
#define BM_R_PWM 47

#define BM_L_ENABLE 45
#define BM_R_ENABLE 46

//Source voltage measurement:

#define VIN_MEASURE 29

//I2C pinout:

#define I2C1_SCL 92
#define I2C1_SDA 93

//SPI pinout:

#define SPI3_SCK 78
#define SPI3_MISO 79
#define SPI3_MOSI 80

//CAN pinout:

#define CAN_RX 70
#define CAN_TX 71

//UART 1 & 2 pinout:

#define UART1_TX 68
#define UART1_RX 69

#define UART2_TX 86
#define UART2_RX 87

//Temperature measurement:

#define TEMP_1 36
#define TEMP_2 35
#define TEMP_3 34
#define TEMP_4 33


//Digital input pinout:

#define IN_1 38
#define IN_2 39
#define IN_3 41
#define IN_4 43
#define IN_5 44
#define IN_6 51
#define IN_7 52
#define IN_8 55
#define IN_9 56
#define IN_10 57
#define IN_11 58
#define IN_12 61

//Digital input pinout:

#define OUT_1 62
#define OUT_2 66
#define OUT_3 65
#define OUT_4 67



#endif /* DEFINES_H_ */

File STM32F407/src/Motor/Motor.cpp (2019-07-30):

/*
 * Motor.cpp
 *
 *  Created on: Jul 17, 2019
 *      Author: mrbr
 */

#include "Motor.h"

void Motor::initPID(const uint16_t& k_p, uint16_t k_d, const uint16_t& k_i)
{
	Kp = k_p;
	Kd = k_d;
	Ki = k_i;
}

void Motor::setRatio(const double& ratio)
{
	this->ratio = ratio;
}

void Motor::setMaxVelocity(const double& max_vel)
{
	maxVel = max_vel;
}

void Motor::setEncoderRange(const uint32_t& range)
{
	encoder.range = range;
}

double Motor::getVelocity()
{
	float velocity = 0;

	if (*encoder.currentCount <= 0.1*encoder.range && encoder.previousCount >= encoder.range*0.9
			&& encoder.previousCount <= encoder.range) {
		velocity = *encoder.currentCount - encoder.previousCount + encoder.range;
	} else if (*encoder.currentCount <= encoder.range && *encoder.currentCount >= encoder.range*0.9
			&& encoder.previousCount <= 0.1*encoder.range) {
		velocity = *encoder.currentCount - encoder.previousCount - encoder.range;
	} else {
		velocity = *encoder.currentCount - encoder.previousCount;
	}

	encoder.previousCount = *encoder.currentCount;
	return currentVel = velocity / encoder.range * 1000 * 2 * 3.1415; //TODO period should be 1kHz
}

void Motor::calcPWM(const double& targetVelocity, const double& currentVelocity)
{

	if(encoder.currentCount == nullptr || mode == FREE)
	{
		pwm = targetVelocity/(maxVel)*MAX_PWM_VALUE;
		return;
	}

	int16_t error = targetVelocity - currentVelocity;
	errorSum += error;
	if (errorSum > MAX_PWM_VALUE)
		errorSum = MAX_PWM_VALUE;
	else if (errorSum < -MAX_PWM_VALUE)
		errorSum = -MAX_PWM_VALUE;

	pwm += Kp*error+Kd*(error-prevError)+Ki*errorSum;
	if (pwm > MAX_PWM_VALUE)
		pwm = MAX_PWM_VALUE;
	else if (pwm < -MAX_PWM_VALUE)
		pwm = -MAX_PWM_VALUE;
	prevError = error;
}

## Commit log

2019-04-27 Added simulation code
    [arm_link.STL, base_link.STL, forearm_link.STL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]
2019-05-04 Finished simulation and PID controllers settings.
    [manipulator.urdf]
2019-05-05 Added velocity controller
    [controllers_effort.yaml, controllers_velocity.yaml, manipulator.urdf]
2019-05-17 Added hardware interface to simulation. Next step- robot<->simulation communication.
    [controllers_velocity.yaml, hardware.yaml]
2019-05-17 Cleanup STM32 folder. Added FreeRTOS dependency
    [manipulator.urdf]
2019-07-27 STM32F407: prepare FreeRTOS based control program
2019-07-28 STM32F407: test program on board
2019-07-29 Simulation: finish hardware interface
    [controllers_effort.yaml, controllers_velocity.yaml, hardware.yaml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]
2019-07-29 STM32F4: add serial comm with simulation
2019-07-30 merge: merge hw_dev to master
    [hardware.yaml]
2019-07-30 manipulator: add sending velocity info to/from robot
